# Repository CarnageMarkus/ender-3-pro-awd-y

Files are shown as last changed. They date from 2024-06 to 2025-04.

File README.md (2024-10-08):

# Ender 3 Pro AWD-Y

Hi, this "AWD" mod adds second stepper motor onto your Y axis, doubling the torque available. As you probably noticed stock bed assembly is quite heavy which significantly limits accelerations. 

With double the torque you will be able to print much faster without compromising on quality!

This mod has been heavily inspired by [LH Stinger](https://github.com/lhndo/LH-Stinger/tree/main)

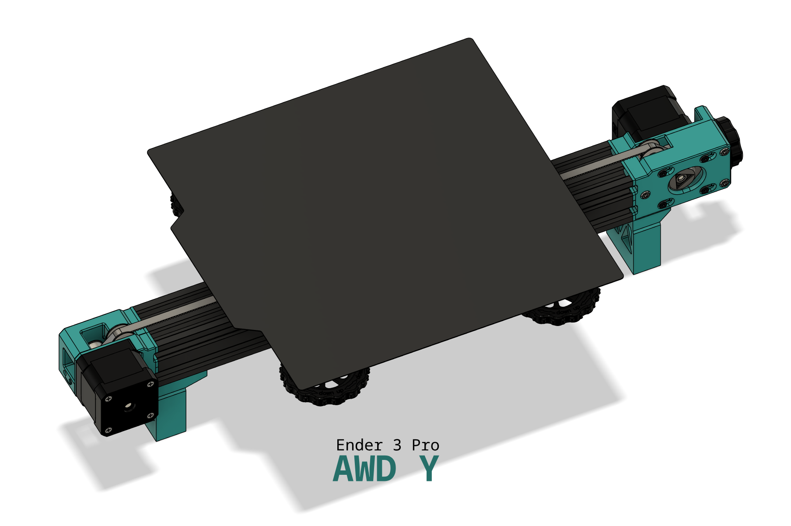
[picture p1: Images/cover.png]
Image of Y axis with two stepper motors
  

[][cc-by-nc-sa]

[cc-by-nc-sa]: http://creativecommons.org/licenses/by-nc-sa/4.0/
[cc-by-nc-sa-image]: https://licensebuttons.net/l/by-nc-sa/4.0/88x31.png
[cc-by-nc-sa-shield]: https://img.shields.io/badge/License-CC%20BY--NC--SA%204.0-lightgrey.svg

## Features
- More torque on Y axis -> better acceleration
- Easy tensioning
- Maximize Y axis travel, as mounts are very low profile (+-280mm)
- Support feet to reduce vibrations and prevent [this issue](https://youtu.be/1tBwaWnOHKY?si=pGgoMI5P9Bu9fiOg&t=324).
- Toothed idlers
- Compatible with [LH Stinger - Ender 3 - CF Carriage](https://discord.com/channels/1167067314781429831/1209625504425054271) as they are very low profile

### Changes over BETA
- 20T GT2 Idlers are now default. I found significant rubbing when using F623 bearings. Belt path has been adjusted.

## FAQ

> Are there build instructions ? 

I am working on them, but for now consult the CAD.

> Can I use single driver / stepper cable splitter ?

This doesn't really make sense, single driver usually does not provide enough to drive two steppers. Same applies to boards with two Z axis cable slots.

> Can I use v-wheels ?

Yes, v-wheels still work. 

> Can I use rigid motor mount to gain clearance for bigger stepper.

Yes, rigid motor mount is designed so that it can be used with stock ender tensioner at the front.

## Rigid Mount 

### BOM

| Part | Quantity | Comment |
| --- | ---: | --- |
| 20T GT2 Idler (**3mm bore**) | 1 | toothed, make sure bore is 3mm |
| 20T GT2 Pulley (**5mm bore**) | 1 | |
| 625 Bearing | 1 | required for double shear, highly recommended (don't confuse with f625) |
| M3x30 SHSC | 4 | |
| M3x7x0.5 Washer/Shim | 6 | 3mm ID x 7 OD x 0.5 Thickness |
| M5x10 BHSC | 4 + 2 | 4 button head screws are required to fit into mounting slots, 2 for support foot |
| M5 T-Nut | 2 | for support foot |
| M5x7x0.5 Washer/Shim | 1 | outer diameter about 7 mm, can be printed as well, needed to prevent pulley rubbing on bearing outside housing which is stationary |
| GT2 2GT Belt | | any of those mods will require longer than stock belt |

## Tensioned Mount

has integrated tensioning mechanism to easily achieve ideal belt tension.

### BOM
| Part | Quantity | Comment |
| --- | ---: | --- |
| 20T GT2 Idler (**3mm bore**) | 1 | toothed, make sure bore is 3mm |
| 20T GT2 Pulley (**5mm bore**) | 1 | |
| 625 Bearing | 1 | required for double shear, highly recommended (don't confuse with f625) |
| M3x30 SHSC | 4 | |
| M3x35 SHSC | 3 | |
| M3x10 SHSC | 2 | required for support foot |
| M3x5L4 heatserts | 3 + 2 | "voron spec" heatserts, 3 for frame rigidity, 2 required for support foot |
| M3x7x0.5 Washer/Shim | 9 | 3mm ID x 7 OD x 0.5 Thickness |
| M5x7x0.5 Washer/Shim | 1 | outer diameter about 7 mm, can be printed as well, needed to prevent pulley rubbing on bearing outside housing which is stationary |
| M5x10 BHSC | 4 | |
| M5 (Self Locking Nut) | 2 | for tensioning mechanism and knob |
| M5x30 BHSC/SHSC | 1 | |
| GT2 2GT Belt | | any of those mods will require longer than stock belt |

## Accessories / Mods

- Bed carriage belt clamps: 
  - https://www.printables.com/model/202019-gt2-belt-fastener (prefer this one as it's stronger)
  - https://www.printables.com/model/250178-gt2-belt-clip-for-kingroon-kp3s (if belt is too short, make sure to clamp with ziptie firmly)

## Important Notes

1. Don't tighten pulley grub screws on rigid mount, until you are sure both steppers turn in right direction. It's safer to configure second driver with one pulley slipping.
2. Do AWD Sync. [macro](https://github.com/lhndo/LH-Stinger/blob/main/Config/Klipper_Config/mymacros.cfg#L773)
3. If motor/belt skips, you need to redo the AWD Sync.
4. After a few days **redo** the tension and AWD Sync, especially if using new belt since it will stretch a bit during first week, resulting in de-synced motors

## Troubleshooting and Build Notes

- Fully tightening the M5x30mm tensioner screw can cause it to scrape the belt, do not overtighten it and check it before running the printer. Use the knob to tension, not the screw itself.
- 5x7x0.5mm shims __or__ 625 *Deep Groove* bearings are required. If using deep groove bearings, larger shims such as 5x10x0.5mm are fine. The goal is for the shim to not rub on the static wall of the bearing.
- Ensure there is a small gap (roughly 1.3mm) between the pulleys and the base of the motors. For the rigid mount, tighten the grub screws and install the motor, and then re-loosen the grub screws for syncing and testing. This ensures the pulley does not get forced up against the motor.
- If you experience periodic resistance when moving the bed, make sure the pulleys are not rubbing on any printed parts.
- Belt tension should be roughly 150hz. [Calculator from LH Stinger](https://docs.google.com/spreadsheets/d/1mgBJEO6Ef19EgX-LgE-lGDI9BayG98oX33mT0myVEUg/edit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)
- Some belt end clips are too loose for the tension/torque of this setup, make sure your belt does not slip through the clip and lose tension.
- If using the printed support feet, make sure they sit evenly. If one is not bearing any weight, shim the bottom with something like electrical tape or reprint it.
- For sensorless homing, use _one_ motor to set up the values. At least in Klipper, stepper_y1 will follow stepper_y by default.

## Credits

- inspiration [LH Stinger](https://github.com/lhndo/LH-Stinger/tree/main) 
- tensioning knob from [KevinAkaSam BeltedZ Mod](https://github.com/kevinakasam/BeltDrivenEnder3)

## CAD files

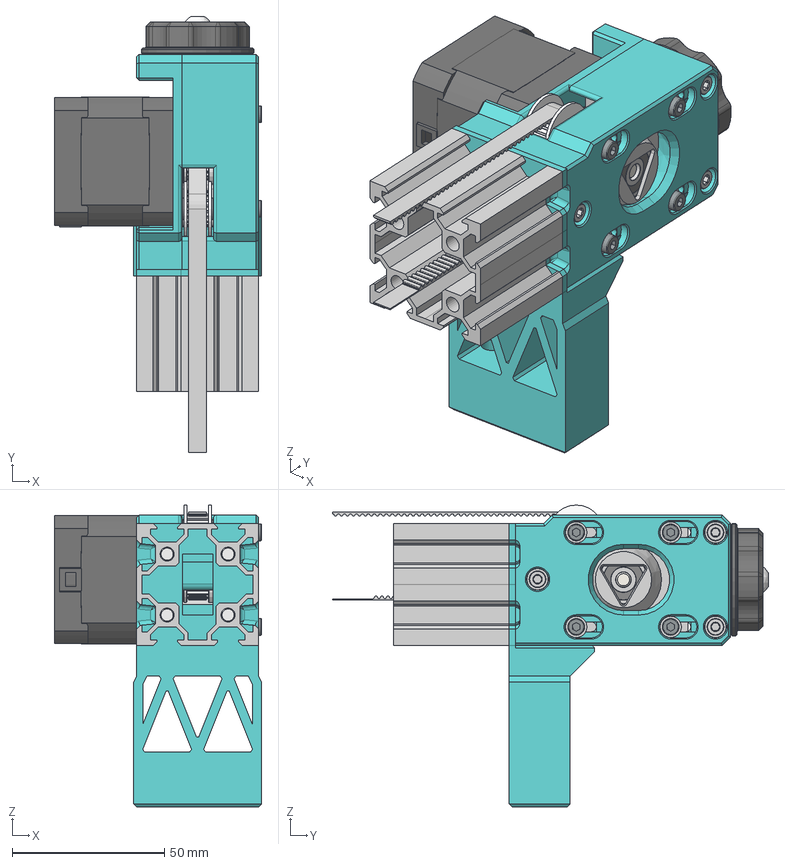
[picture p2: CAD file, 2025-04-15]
CAD/Ender 3 Pro AWD Y Tensioned v19.step
68.0 x 143.1 x 99.1 mm
4040 Extrusion Dummy
NEMA17 (Black)
M3x30SHSC x 4
Timing Pulley - 2GT-20T - For 6mm Belt - 5mm Bore
M5 Shim 0.5mm
Bearing 625 2RS
POWGE 2GT 20T B3 Idler
M5x10 BHSC x 4
Washer M3 7mm 0.5mm x 9
M5 Self-locking nut x 2
M5X30 BHSC
KevinAkaSam Tensioner Ring
M3x35 SHSC x 3
M3x4 Threaded Insert x 5
M3x10 SHSC x 2
belt

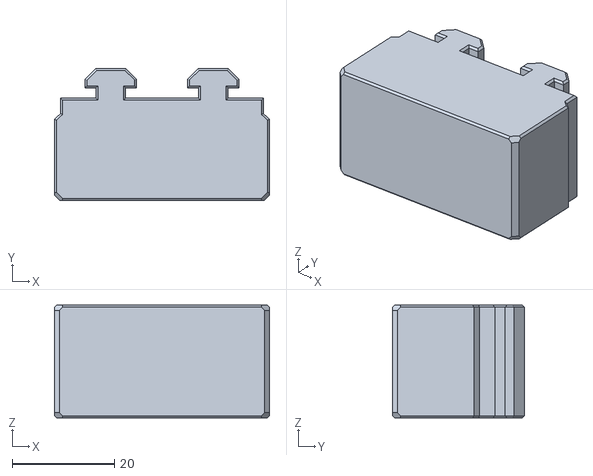
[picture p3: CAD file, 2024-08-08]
STL/Misc/side extrusion support foot x4.stl
42.0 x 25.8 x 22.0

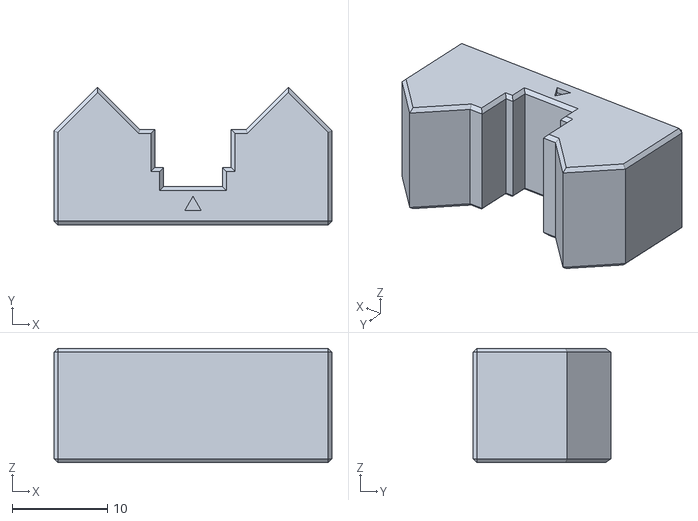
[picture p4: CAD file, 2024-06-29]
STL/Rigid/belt alignment tool.stl
29.2 x 14.4 x 12.0

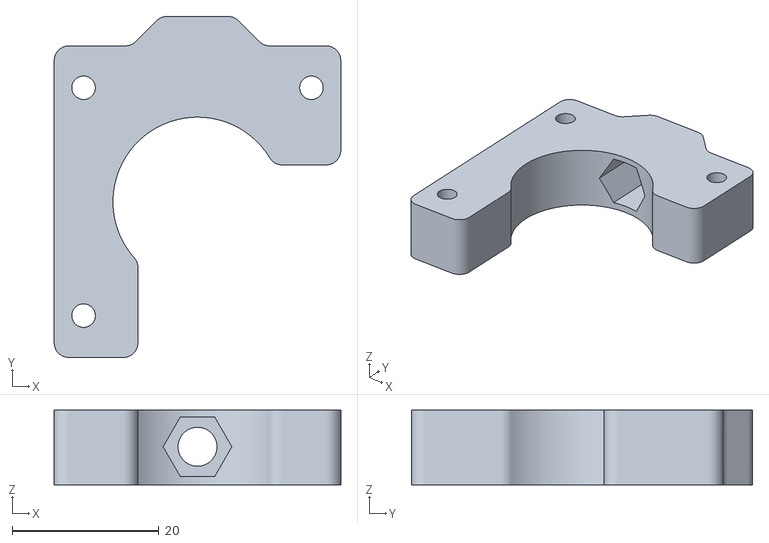
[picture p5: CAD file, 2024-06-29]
STL/Tensioned/tensioner B.stl
39.0 x 46.4 x 10.2

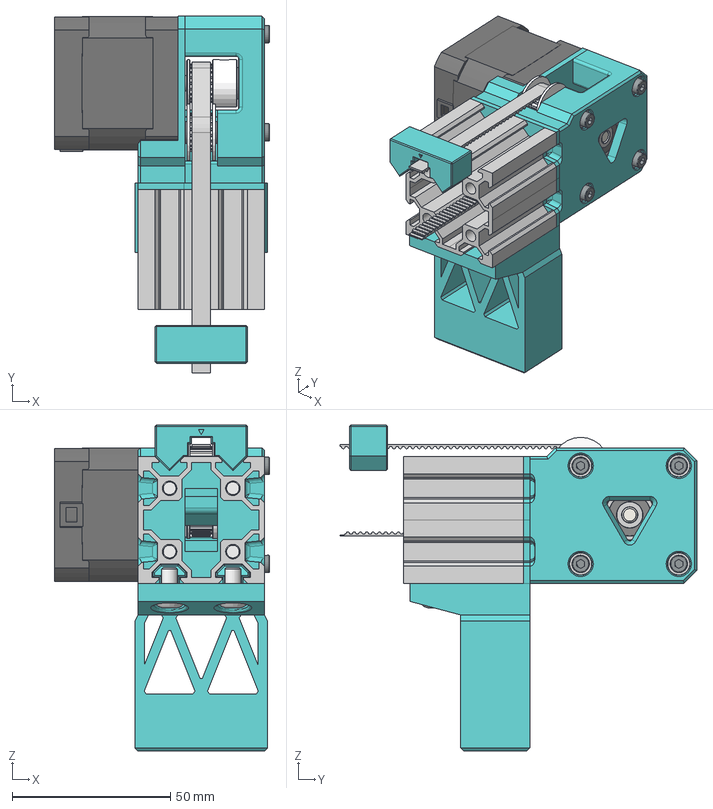
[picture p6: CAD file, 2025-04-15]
CAD/Ender 3 Pro AWD Y Rigid v33.step
68.0 x 112.7 x 103.0 mm
4040 Extrusion Dummy
NEMA17 (Black)
M3x30SHSC x 4
Timing Pulley - 2GT-20T - For 6mm Belt - 5mm Bore
M5 Shim 0.5mm
Bearing 625 2RS
POWGE 2GT 20T B3 Idler
M5x10 BHSC x 6
Washer M3 7mm 0.5mm x 6
belt

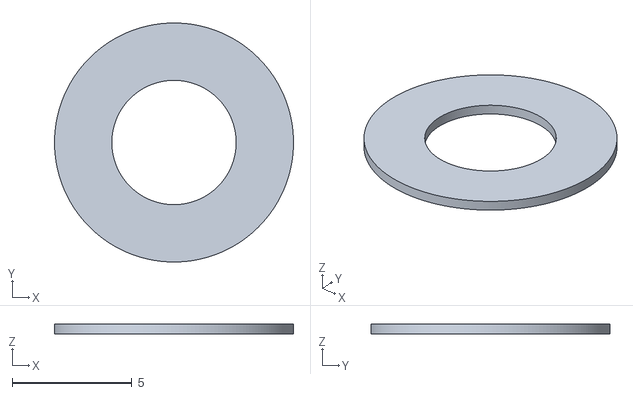
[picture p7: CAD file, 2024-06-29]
STL/Misc/Printed M5 Shim.stl
10.00 x 10.00 x 0.4

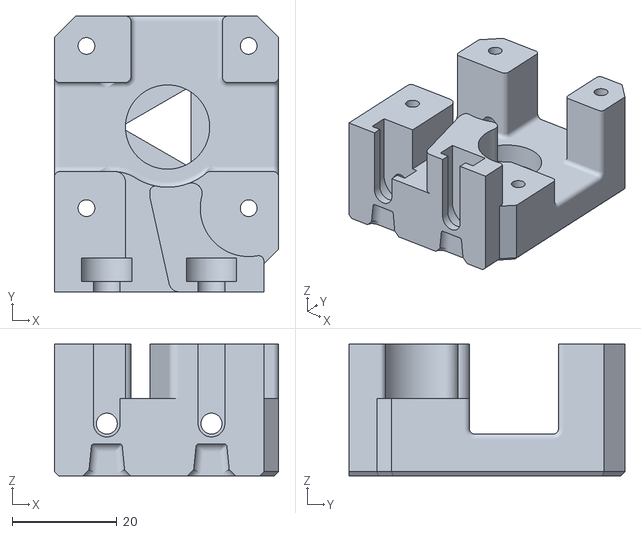
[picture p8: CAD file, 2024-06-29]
STL/Rigid/Frame A.stl
42.8 x 52.7 x 25.2

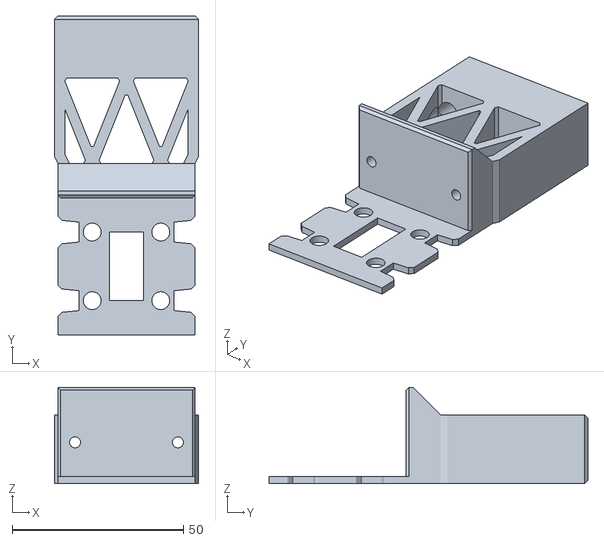
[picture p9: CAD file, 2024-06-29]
STL/Tensioned/support foot.stl
42.0 x 93.0 x 28.0

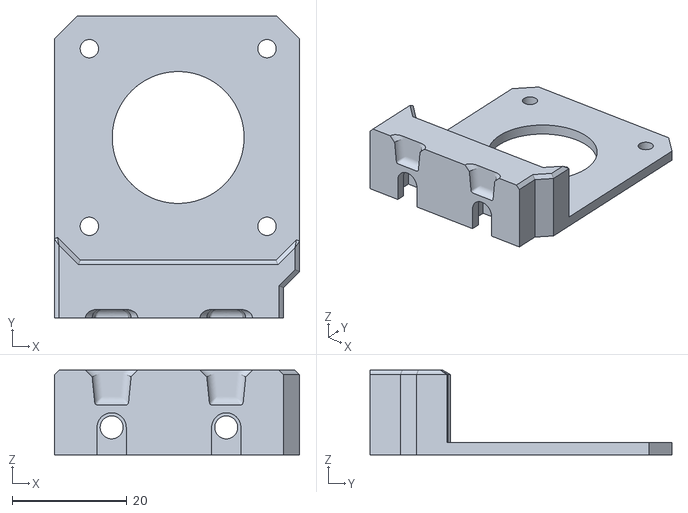
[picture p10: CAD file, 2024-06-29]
STL/Rigid/Frame B.stl
42.8 x 52.7 x 14.8

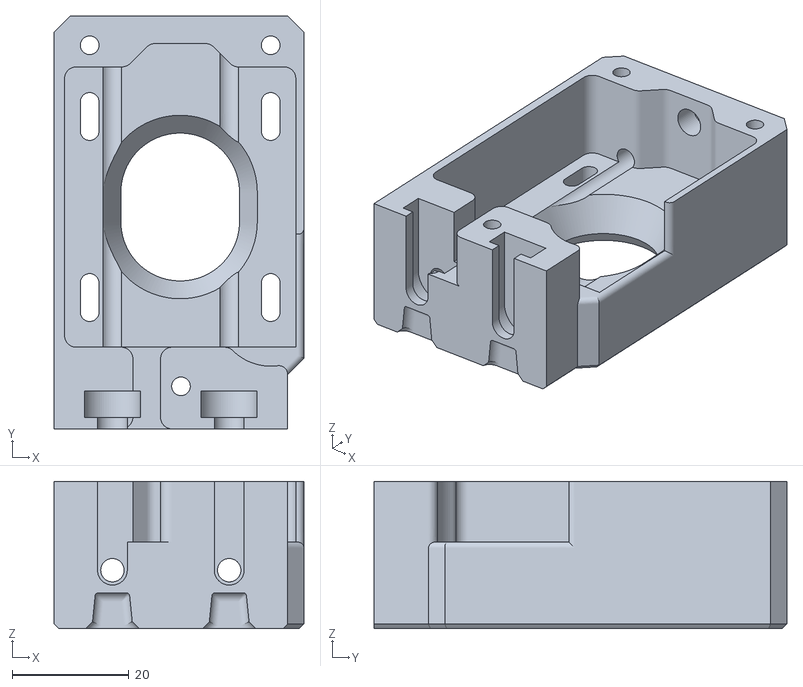
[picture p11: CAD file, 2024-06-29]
STL/Tensioned/Frame A.stl
42.8 x 70.7 x 25.2

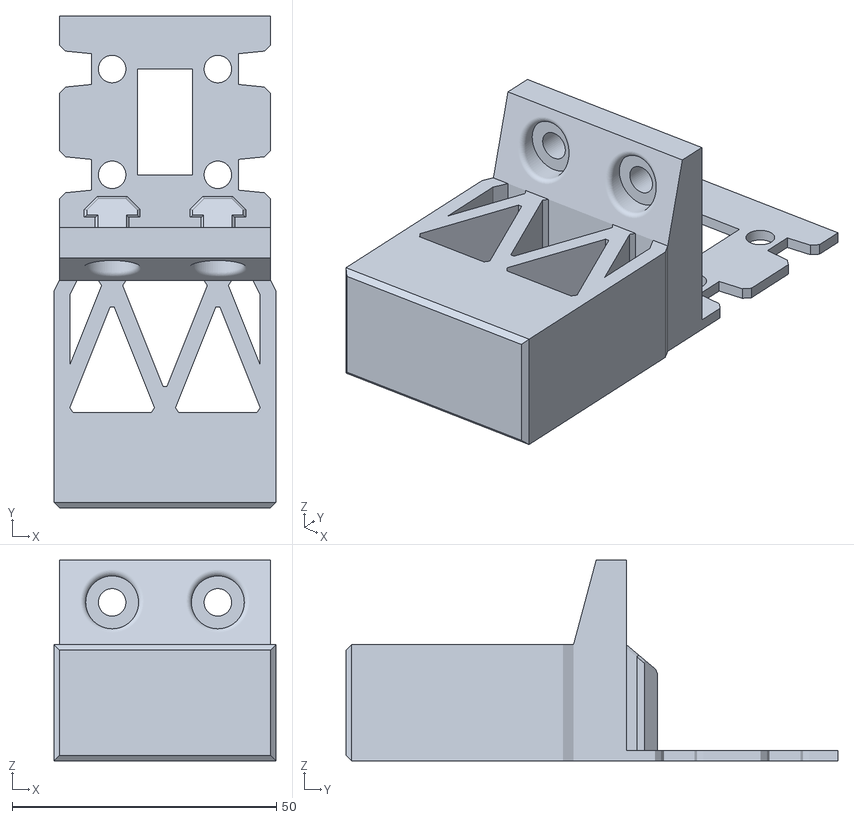
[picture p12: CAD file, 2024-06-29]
STL/Rigid/support foot.stl
42.0 x 93.0 x 38.0

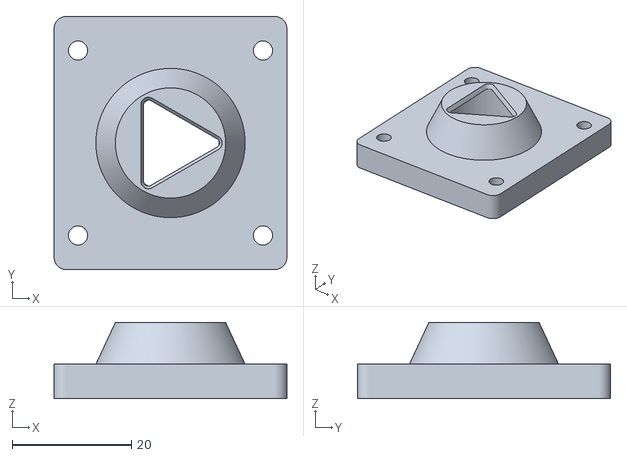
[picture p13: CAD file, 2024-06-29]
STL/Tensioned/tensioner A.stl
39.0 x 42.4 x 12.8

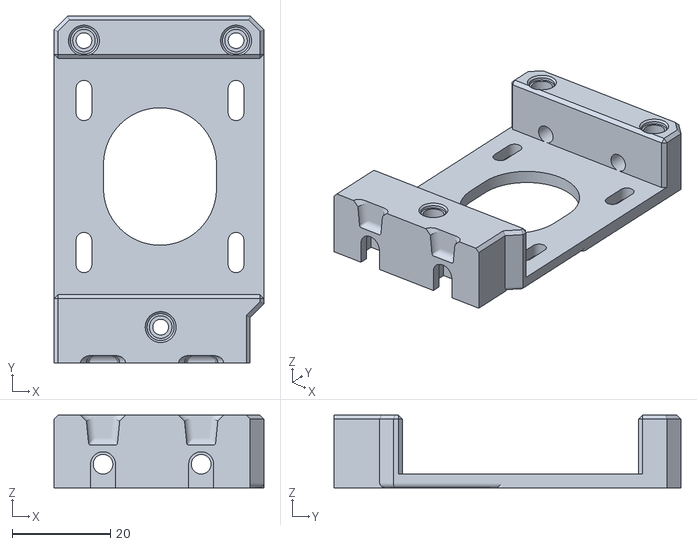
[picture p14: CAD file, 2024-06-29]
STL/Tensioned/Frame B.stl
42.8 x 70.7 x 14.8

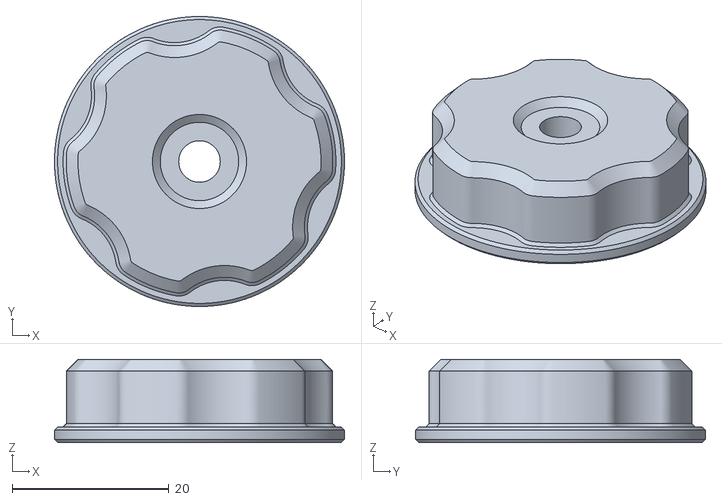
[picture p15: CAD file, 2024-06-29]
STL/Tensioned/KevinAkaSam Tensioner Ring.stl
37.0 x 37.0 x 10.6

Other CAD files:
OLD/F623/CAD/Ender 3 Pro AWD Y Rigid (f623)(old) v11.f3z

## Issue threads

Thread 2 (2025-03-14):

There are no STEP files

RubberEyes, 2025-03-14:
I understand that the parts are designed in Fusion360, and that's the CAD that is being made available, but it's proprietary and very expensive. Adding STEP files would make the CAD files more accessible for everyone.

RubberEyes, 2025-04-16:
This has been corrected

Closed 2025-04-16.

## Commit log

2024-06-28 Initial release files ?
    [Ender 3 Pro AWD Y Rigid (f623)(old) v11.f3z, Frame A.stl, Frame B.stl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]
2024-06-28 add info about new belt requirement
2024-06-29 fix 20T idler with correct bore, update readme, update stls
    [Frame A.stl, Frame B.stl, belt alignment tool.stl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]
2024-06-29 added tensioner knob
    [KevinAkaSam Tensioner Ring.stl]
2024-06-29 update cad with tensioner
2024-06-29 update clearances for m5 shim
    [Frame A.stl, Frame B.stl, Printed M5 Shim.stl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]
2024-06-29 update bom
2024-08-08 add side extrusion support foot.
    [side extrusion support foot x4.stl]
2025-04-15 Added step files
    [Ender 3 Pro AWD Y Rigid v33.step, Ender 3 Pro AWD Y Tensioned v19.step]

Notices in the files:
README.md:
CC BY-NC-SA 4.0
